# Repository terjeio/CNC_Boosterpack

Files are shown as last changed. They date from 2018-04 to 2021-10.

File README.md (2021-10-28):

## CNC BoosterPack for Texas Instruments LaunchPads

A BoosterPack that provides 3-axis motor support for some LaunchPads, driver code for [grblHAL](https://github.com/grblHAL) is available for [MSP432P401R](https://github.com/grblHAL/MSP432P401R), [MSP432E401Y](https://github.com/grblHAL/MSP432E401Y), Tiva C\([EK-TM4C123GXL](https://github.com/grblHAL/TM4C123) and [EK-TM4C1294XL](https://github.com/grblHAL/TM4C1294)\) and [MSP430F5529](https://github.com/grblHAL/MSP430F5529).

Prototype "motherboards" has been made for ESP32, STM32F103 \(Bluepill\) and SAMD21 \(MKRZERO\) development boards allowing the CNC BoosterPack to be used with these, I may add them later.

**NOTE:** design files are in [KiCad 5](http://www.kicad.org/) format!

**Features:**

* 3-axis motor support with separate enable for Z and X,Y \(X,Y has a single enable signal\). Trinamic version has separate enable for all axes.

* On-board sockets for Polulu style motor driver modules (A4998 and DRV8825). Separate version for Trinamic drivers \(initially TMC2130\).

* Opto-coupled limit and signal inputs (X, Y, Z, Probe, Reset, Door, Feed Hold and Cycle Start) with 5V drive voltage.

* Opto-coupled signal outputs \(Spindle on, Spindle direction, Flood and Mist\) with jumper selectable drive voltage \(5V internal or externally supplied\). Outputs are open drain \(2N7002\) capable of draining 200mA \(up to 300mA depending on 2N7002 variant\), enough to drive most relays directly. Outputs can be made opto-isolated via jumper settings.

* PWM output for spindle speed control, unbuffered.

* One I2C port with jumper selectable drive voltage \(3.3V or 5V\). This is complemented with a GPIO pin that may be used as an interrupt source, eg. for a I2C-based keypad.

* Two GPIO ports, one with four pins and one with two. Two-pin GPIO-port may be used as secondary UART input, eg. for MPG control.

* Optional on-board EEPROM for persistent storage of settings.

Separate version for Trinamic TMC2130 drivers added, onboard I2C \<\> SPI bridge for driver control. 4-layer board.
A small batch of the Trinamic version has been made, good progress made on [I2C \<\> SPI bridge firmware](https://github.com/terjeio/Trinamic_TMC2130_I2C_SPI_Bridge). Driver monitoring has been delegated to the bridge prosessor, a couple of additional datagrams will be implemented to facilitate support for this in the grblHAL-driver - first out will be for MSP432.

Both designs are now reduced in size so two boards may be mounted on TMC129 or MSP432E401Y LaunchPads for controlling up to 6-axes. 

I have a few bare boards for sale at cost if anyone is interested. The "standard - non-Trinamic" boards I have available is the larger revision 1.0. 

Detailed documentation to follow.

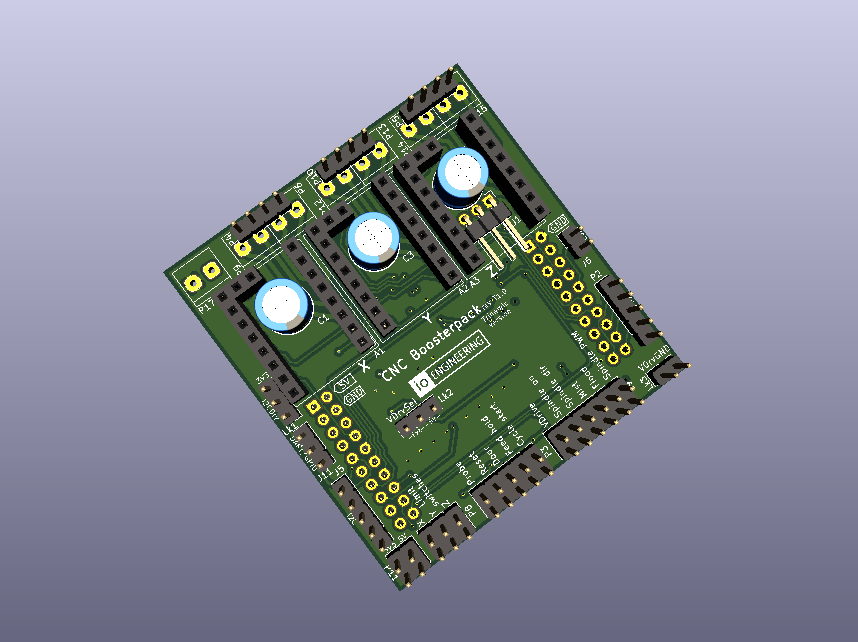
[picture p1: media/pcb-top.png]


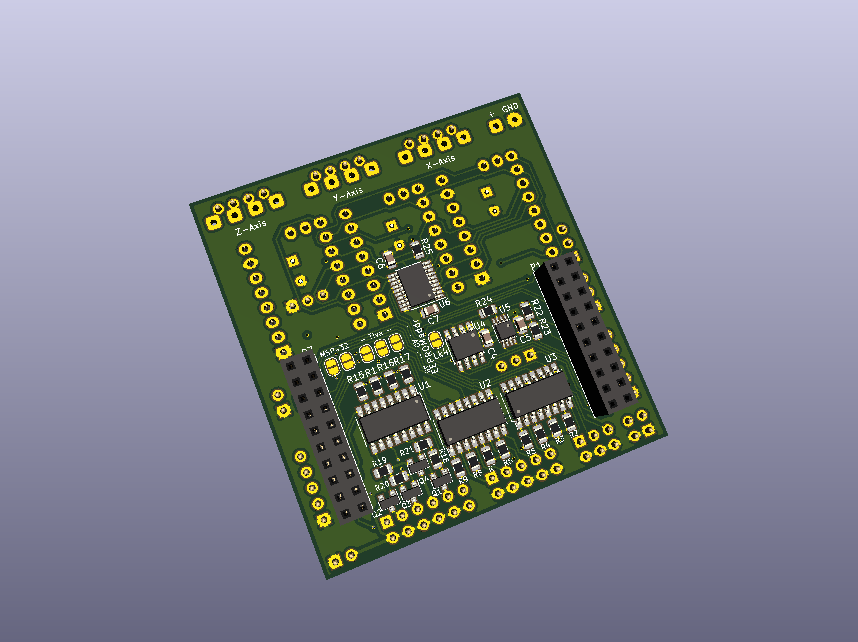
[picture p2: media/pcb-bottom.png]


---

## Bonus design: Polulu style motor driver "dummy"

* with buffered \(open drain\) outputs for external drivers like DQ542MA.

**NOTE:** output signals are inverted

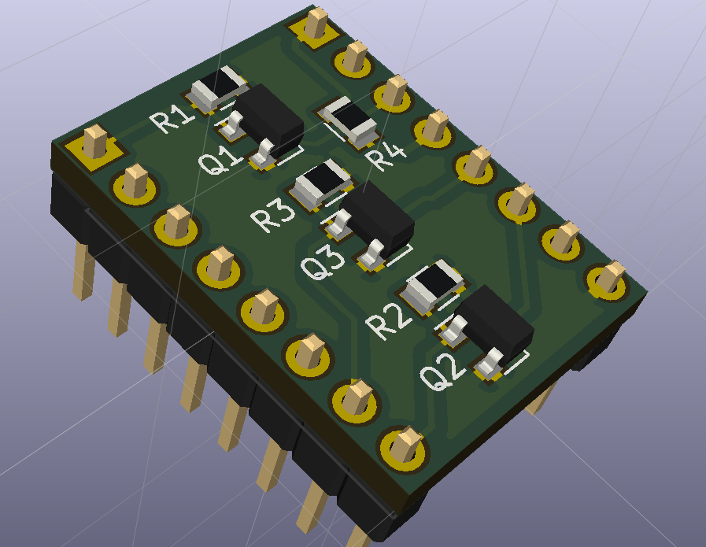
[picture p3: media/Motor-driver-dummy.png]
Dummy PCB


---

## Bonus design II: BLDC Motor driver board, 3.3V (or 5V) PWM to 0 - 10V DC conversion

* with opto-coupled PWM input.

* PCB layout matches WSS55 BLDC Driver connector

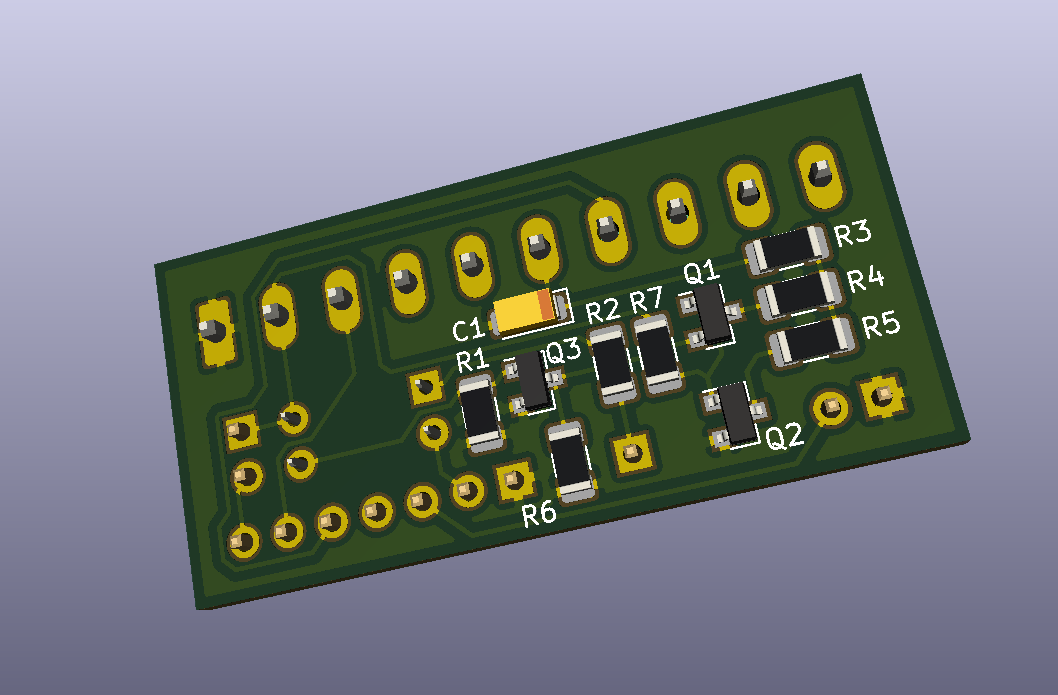
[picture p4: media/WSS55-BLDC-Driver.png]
BLDC Motor Driver PCB


---
2021-10-28

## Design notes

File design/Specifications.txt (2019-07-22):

CNC BoosterPack Rev 1.0

3-axis CNC addon for Texas Instruments LaunchPads with 40 pin interface.

Support for my HALified version of GRBL (based on 1.1), currently drivers has been made for MSP432 (black version), Tiva C and MSP430F2955.
NOTE: firmware is built with CCS 6.1, MSP432 driver is 100% CMSIS based.

Opto-coupled inputs, NC switches recommended.

Opto-coupled outputs with 200mA open drain drive for spindle on, spindle direction, flood and mist.
Can drive most relays and solenoids directly. 
Output section can be powered from internal 3V3 or 5V source, or from external source.
If powered from external source outputs can be made opto-isolated via jumper setting.

PWM-output for spindle speed currently directly connected to MCU pin (could be changed to open drain).

I2C (IIC) interface with selectable voltage level (3V3 or 5V) via level shifter, dedicated interrupt input.
I2C pinout compatible with my 4x4 keyboard project, supports jogging etc.

Optional EEPROM for configuration settings for MCUs with no internal EEPROM.

Polulu 8825 motor driver breakout board compatible. Fault signal routed to GPIO input.

Considered for later revision:

Break out SPI interface and add full support for Trinamic motor drivers.
Optional (SPI) DAC for motor speed (laser power) control.

This might require a 4-layer PCB and also solving the pinout cabal...

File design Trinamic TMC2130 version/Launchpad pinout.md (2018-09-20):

 ## LaunchPad GRBL pin assignments for CNC Boosterpack rev1.0

 ## Tiva C \(TM4C123G\)

```
                      3v3 [] [] VBUS (5v)             Limit Z PF2 [] [] GND
                      PB5 [] [] GND                   Limit Y PF3 [] [] PB2 Spindle PWM
       UART2 RX/GPIO4 PB0 [] [] PD0                     Reset PB3 [] [] PE0 Limit X
       UART2 TX/GPIO5 PB1 [] [] PD1 Step X        Safety Door PC4 [] [] PF0 Stepper disable Z
  Keypad strobe/GPIO6 PE4 [] [] PD2 Step Y          Feed Hold PC5 [] [] RST
                      PE5 [] [] PD3 Step Z        Cycle Start PC6 [] [] PB7 Dir X
                Dir Z PB4 [] [] PE1 Stepper disable XY        PC7 [] [] PB6 Dir Y
                Probe PA5 [] [] PE2 Spindle enable      Flood PD6 [] [] PA4 GPIO1
               I2CSCL PA6 [] [] PE3 Spindle direction    Mist PD7 [] [] PA3 GPIO2
               I2CSDA PA7 [] [] PF1                 RTS/GPIO0 PF4 [] [] PA2 GPIO3
```
__NOTE__: Remove R9 and R10!

With shorts - Limit X (R10): PE0 -> PF1, Reset (R11): PB3 -> PC7

## Tiva C \(TM4C1294\) Boosterpack1

```
                      3v3 [] [] VBUS (5v)             Limit Z PF1 [] [] GND
                      PE4 [] [] GND                   Limit Y PF2 [] [] PM3 Spindle PWM
       UART7 RX/GPIO4 PC4 [] [] PE0                     Reset PF3 [] [] PH2 Limit X
       UART7 TX/GPIO5 PC5 [] [] PE1 Step X        Safety Door PG0 [] [] PH3 Stepper disable Z
  Keypad strobe/GPIO6 PC6 [] [] PE2 Step Y          Feed Hold PL4 [] [] RST
                      PE5 [] [] PE3 Step Z        Cycle Start PL5 [] [] PD1 Dir X
                Dir Z PD3 [] [] PD7 Stepper disable XY        PL0 [] [] PD0 Dir Y
                Probe PC7 [] [] PA6 Spindle enable      Flood PL1 [] [] PN2 GPIO1
               I2CSCL PB2 [] [] PM4 Spindle direction    Mist PL2 [] [] PN3 GPIO2
               I2CSDA PB3 [] [] PM5                 RTS/GPIO0 PL3 [] [] PP3 GPIO3
```

## Tiva C \(TM4C1294\) Boosterpack2

```
                      3v3 [] [] VBUS (5v)             Limit Z PG1 [] [] GND
                      PD2 [] [] GND                   Limit Y PK4 [] [] PM7 Spindle PWM
       UART6 RX/GPIO4 PP0 [] [] PB4                     Reset PK5 [] [] PP5 Limit X
       UART6 TX/GPIO5 PP1 [] [] PB5 Step X        Safety Door PM0 [] [] PA7 Stepper disable Z
  Keypad strobe/GPIO6 PD4 [] [] PK0 Step Y          Feed Hold PM1 [] [] RST
                      PD5 [] [] PK1 Step Z        Cycle Start PM2 [] [] PQ2 Dir X
                Dir Z PQ0 [] [] PK2 Stepper disable XY        PH0 [] [] PQ3 Dir Y
                Probe PP4 [] [] PK3 Spindle enable      Flood PH1 [] [] PP3 GPIO1
               I2CSCL PN5 [] [] PA4 Spindle direction    Mist PK6 [] [] PQ1 GPIO2
               I2CSDA PN4 [] [] PA5                 RTS/GPIO0 PK7 [] [] PM6 GPIO3
```

## MSP430F5529

```
                      3v3 [] [] VBUS (5v)            Limit Z P2.5 [] [] GND
                     P6.5 [] [] GND                  Limit Y P2.4 [] [] P2.0 Spindle PWM
      UART2 RX/GPIO4 P3.4 [] [] P6.0                   Reset P1.5 [] [] P2.2 Limit X
      UART2 TX/GPIO5 P3.3 [] [] P6.1 Step X      Safety Door P1.4 [] [] P7.4 Stepper disable Z
 Keypad strobe/GPIO6 P1.6 [] [] P6.2 Step Y        Feed Hold P1.3 [] [] RST
                     P6.6 [] [] P6.3 Step Z      Cycle Start P1.2 [] [] P3.0 Dir X
               Dir Z P3.2 [] [] P6.4 Stepper disable XY      P4.3 [] [] P3.1 Dir Y
               Probe P2.7 [] [] P7.0 Spindle enable    Flood P4.0 [] [] P2.6 GPIO1
              I2CSCL P4.2 [] [] P3.6 Spindle direction  Mist P3.7 [] [] P2.3 GPIO2
              I2CSDA P4.1 [] [] P3.5               RTS/GPIO0 P8.2 [] [] P8.1 GPIO3
```

## MSP432P401R

```
                      3v3 [] [] VBUS (5v)            Limit Z P2.7 [] [] GND
                     P6.0 [] [] GND                  Limit Y P2.6 [] [] P2.5 Spindle PWM
      UART2 RX/GPIO4 P3.2 [] [] P6.1                   Reset P2.4 [] [] P3.0 Limit X
      UART2 TX/GPIO5 P3.3 [] [] P4.0 Step X      Safety Door P5.6 [] [] P5.7 Stepper disable Z
 Keypad strobe/GPIO6 P4.1 [] [] P4.2 Step Y        Feed Hold P6.6 [] [] RST
                     P4.3 [] [] P4.4 Step Z      Cycle Start P6.7 [] [] P1.6 Dir X
               Dir Z P1.5 [] [] P4.5 Stepper disable XY      P2.3 [] [] P1.7 Dir Y
               Probe P4.6 [] [] P4.7 Spindle enable    Flood P5.1 [] [] P5.0 GPIO1
              I2CSCL P6.5 [] [] P5.4 Spindle direction  Mist P3.5 [] [] P5.2 GPIO2
              I2CSDA P6.4 [] [] P5.5               RTS/GPIO0 P3.7 [] [] P3.6 GPIO3
```
With shorts - Reset (R12): P2.4 -> P6.0, Safety Door (R13): P5.6 -> P6.1, Limit X (R14): P3.0 -> P2.3

---

## Stepper drivers

### A4998 - requires 3V3 on VDD pin
```
MS1     MS2     MS3     Microstep resolution
Low 	Low 	Low 	Full step
High 	Low 	Low 	Half step
Low 	High 	Low 	Quarter step
High 	High 	Low 	Eighth step
High 	High 	High 	Sixteenth step
```
https://www.pololu.com/product/1182

### DRV8825
```
MS1     MS2     MS3     Microstep resolution
Low 	Low 	Low 	Full step
High 	Low 	Low 	Half step
Low 	High 	Low 	1/4 step
High 	High 	Low 	1/8 step
Low 	Low 	High 	1/16 step
High 	Low 	High 	1/32 step
Low 	High 	High 	1/32 step
High 	High 	High 	1/32 step
```
https://www.pololu.com/product/2133

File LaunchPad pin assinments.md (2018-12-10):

 ## LaunchPad grblHAL pin assignments for CNC Boosterpack rev1.0

 ### Tiva C \(TM4C123G\)

```
                      3v3 [] [] VBUS (5v)             Limit Z PF2 [] [] GND
                      PB5 [] [] GND                   Limit Y PF3 [] [] PB2 Spindle PWM
       UART2 RX/GPIO4 PB0 [] [] PD0                     Reset PB3 [] [] PE0 Limit X
       UART2 TX/GPIO5 PB1 [] [] PD1 Step X        Safety Door PC4 [] [] PF0 Stepper disable Z
  Keypad strobe/GPIO6 PE4 [] [] PD2 Step Y          Feed Hold PC5 [] [] RST
                      PE5 [] [] PD3 Step Z        Cycle Start PC6 [] [] PB7 Dir X
                Dir Z PB4 [] [] PE1 Stepper disable XY        PC7 [] [] PB6 Dir Y
                Probe PA5 [] [] PE2 Spindle enable      Flood PD6 [] [] PA4 GPIO1
               I2CSCL PA6 [] [] PE3 Spindle direction    Mist PD7 [] [] PA3 GPIO2
               I2CSDA PA7 [] [] PF1                 RTS/GPIO0 PF4 [] [] PA2 GPIO3
```
__NOTE__: Remove R9 and R10! Q1, Q2 and Q3 may also be removed (depending on limit switches configuration) as they have inbuilt pull down resistors.

With shorts - Limit X (R10): PE0 -> PF1, Reset (R11): PB3 -> PC7

---

### Tiva C \(TM4C1294\) and MSP432E401Y
 
 Boosterpack 1

```
                      3v3 [] [] VBUS (5v)             Limit Z PF1 [] [] GND
                      PE4 [] [] GND                   Limit Y PF2 [] [] PM3 Spindle PWM
       UART7 RX/GPIO4 PC4 [] [] PE0                     Reset PF3 [] [] PH2 Limit X
       UART7 TX/GPIO5 PC5 [] [] PE1 Step X        Safety Door PG0 [] [] PH3 Stepper disable Z
  Keypad strobe/GPIO6 PC6 [] [] PE2 Step Y          Feed Hold PL4 [] [] RST
                      PE5 [] [] PE3 Step Z        Cycle Start PL5 [] [] PD1 Dir X
                Dir Z PD3 [] [] PD7 Stepper disable XY        PL0 [] [] PD0 Dir Y
                Probe PC7 [] [] PA6 Spindle enable      Flood PL1 [] [] PN2 GPIO1
               I2CSCL PB2 [] [] PM4 Spindle direction    Mist PL2 [] [] PN3 GPIO2
               I2CSDA PB3 [] [] PM5                 RTS/GPIO0 PL3 [] [] PP3 GPIO3
```
Boosterpack 2, ABC-axes

```
                      3v3 [] [] VBUS (5v)             Limit B PG1 [] [] GND
                      PD2 [] [] GND                   Limit A PK4 [] [] PM7 Spindle PWM
          U6 RX/GPIO4 PP0 [] [] PB4                     Reset PK5 [] [] PP5 Limit C
          U6 TX/GPIO5 PP1 [] [] PB5 Step C        Safety Door PM0 [] [] PA7 Stepper disable B
  Keypad strobe/GPIO6 PD4 [] [] PK0 Step A          Feed Hold PM1 [] [] RST
                      PD5 [] [] PK1 Step B        Cycle Start PM2 [] [] PQ2 Dir C (PA3)
                Dir B PQ0 [] [] PK2 Stepper disable AC        PH0 [] [] PQ3 Dir A (PA2)
                Probe PP4 [] [] PK3 Spindle enable      Flood PH1 [] [] PP3 GPIO1
               I2CSCL PN5 [] [] PA4 Spindle direction    Mist PK6 [] [] PQ1 GPIO2
               I2CSDA PN4 [] [] PA5                 RTS/GPIO0 PK7 [] [] PM6 GPIO3
```

Boosterpack2, SD Card - TM4C1294 \(SSI0\)

```
                      3v3 [] [] VBUS (5v)                     PG1 [] [] GND
                      PD2 [] [] GND                           PK4 [] [] PM7
                      PP0 [] [] PB4                           PK5 [] [] PP5 CS
                      PP1 [] [] PB5                           PM0 [] [] PA7
                      PD4 [] [] PK0                           PM1 [] [] RST
                      PD5 [] [] PK1                           PM2 [] [] PQ2
                      PQ0 [] [] PK2                           PH0 [] [] PQ3 CLK        
                      PP4 [] [] PK3                           PH1 [] [] PP3
                      PN5 [] [] PA4 MOSI                      PK6 [] [] PQ1
                      PN4 [] [] PA5 SOMI                      PK7 [] [] PM6
```

Boosterpack2, SD Card - MSP432E401Y \(SSI3\)

```
                      3v3 [] [] VBUS (5v)                     PG1 [] [] GND
                      PD2 [] [] GND                           PK4 [] [] PM7
                      PP0 [] [] PB4                           PK5 [] [] PP5 CS
                      PP1 [] [] PB5                           PM0 [] [] PA7
                      PD4 [] [] PK0                           PM1 [] [] RST
                      PD5 [] [] PK1                           PM2 [] [] PQ2 MOSI
                  CLK PQ0 [] [] PK2                           PH0 [] [] PQ3 SOMI
                      PP4 [] [] PK3                           PH1 [] [] PP3
                      PN5 [] [] PA4                           PK6 [] [] PQ1
                      PN4 [] [] PA5                           PK7 [] [] PM6
```

---

### MSP430F5529

```
                      3v3 [] [] VBUS (5v)            Limit Z P2.5 [] [] GND
                     P6.5 [] [] GND                  Limit Y P2.4 [] [] P2.0 Spindle PWM
      UART2 RX/GPIO4 P3.4 [] [] P6.0                   Reset P1.5 [] [] P2.2 Limit X
      UART2 TX/GPIO5 P3.3 [] [] P6.1 Step X      Safety Door P1.4 [] [] P7.4 Stepper disable Z
 Keypad strobe/GPIO6 P1.6 [] [] P6.2 Step Y        Feed Hold P1.3 [] [] RST
                     P6.6 [] [] P6.3 Step Z      Cycle Start P1.2 [] [] P3.0 Dir X
               Dir Z P3.2 [] [] P6.4 Stepper disable XY      P4.3 [] [] P3.1 Dir Y
               Probe P2.7 [] [] P7.0 Spindle enable    Flood P4.0 [] [] P2.6 GPIO1
              I2CSCL P4.2 [] [] P3.6 Spindle direction  Mist P3.7 [] [] P2.3 GPIO2
              I2CSDA P4.1 [] [] P3.5               RTS/GPIO0 P8.2 [] [] P8.1 GPIO3
```

---

### MSP432P401R

```
                      3v3 [] [] VBUS (5v)            Limit Z P2.7 [] [] GND
                     P6.0 [] [] GND                  Limit Y P2.6 [] [] P2.5 Spindle PWM
      UART2 RX/GPIO4 P3.2 [] [] P6.1                   Reset P2.4 [] [] P3.0 Limit X
      UART2 TX/GPIO5 P3.3 [] [] P4.0 Step X      Safety Door P5.6 [] [] P5.7 Stepper disable Z
 Keypad strobe/GPIO6 P4.1 [] [] P4.2 Step Y        Feed Hold P6.6 [] [] RST
                     P4.3 [] [] P4.4 Step Z      Cycle Start P6.7 [] [] P1.6 Dir X
               Dir Z P1.5 [] [] P4.5 Stepper disable XY      P2.3 [] [] P1.7 Dir Y
               Probe P4.6 [] [] P4.7 Spindle enable    Flood P5.1 [] [] P5.0 GPIO1
              I2CSCL P6.5 [] [] P5.4 Spindle direction  Mist P3.5 [] [] P5.2 GPIO2
              I2CSDA P6.4 [] [] P5.5               RTS/GPIO0 P3.7 [] [] P3.6 GPIO3
```
With shorts - Reset (R12): P2.4 -> P6.0, Safety Door (R13): P5.6 -> P6.1, Limit X (R14): P3.0 -> P2.3

---

### Stepper drivers

#### A4998

**NOTE:** requires 3V3 on VDD pin supplied from GPIO output

```
MS1     MS2     MS3     Microstep resolution
Low 	Low 	Low 	Full step
High 	Low 	Low 	Half step
Low 	High 	Low 	Quarter step
High 	High 	Low 	Eighth step
High 	High 	High 	Sixteenth step
```
https://www.pololu.com/product/1182

#### DRV8825
```
MS1     MS2     MS3     Microstep resolution
Low 	Low 	Low 	Full step
High 	Low 	Low 	Half step
Low 	High 	Low 	1/4 step
High 	High 	Low 	1/8 step
Low 	Low 	High 	1/16 step
High 	Low 	High 	1/32 step
Low 	High 	High 	1/32 step
High 	High 	High 	1/32 step
```
https://www.pololu.com/product/2133

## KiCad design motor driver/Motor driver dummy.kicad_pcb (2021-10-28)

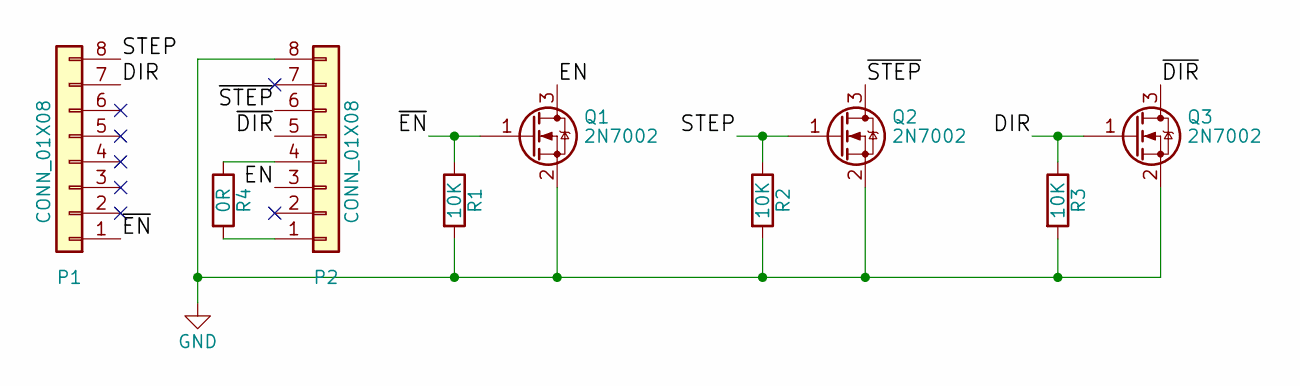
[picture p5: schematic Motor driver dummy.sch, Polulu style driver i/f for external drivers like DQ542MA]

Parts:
P1, P2: CONN_01X08; PinHeader_1x08_P2.54mm_Vertical
Q1, Q2, Q3: 2N7002; SOT-23
R1, R2, R3: 10K; R_0805_2012Metric
R4: 0R; R_0805_2012Metric

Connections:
/DIR: P1.7, Q3.1 (G), R3.1
/EN: P2.3, Q1.3 (D)
/STEP: P1.8, Q2.1 (G), R2.1
/~DIR: P2.5, Q3.3 (D)
/~EN: P1.1, Q1.1 (G), R1.1
/~STEP: P2.6, Q2.3 (D)
GND: P2.8, Q1.2 (S), Q2.2 (S), Q3.2 (S), R1.2, R2.2, R3.2
unnamed: P2.1, R4.2
unnamed: P2.4, R4.1

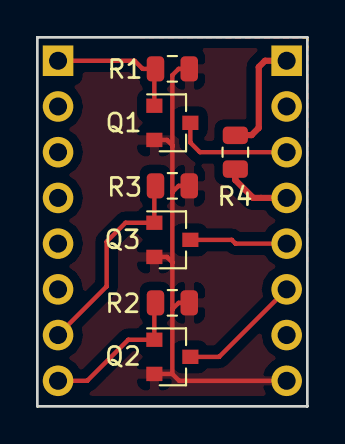
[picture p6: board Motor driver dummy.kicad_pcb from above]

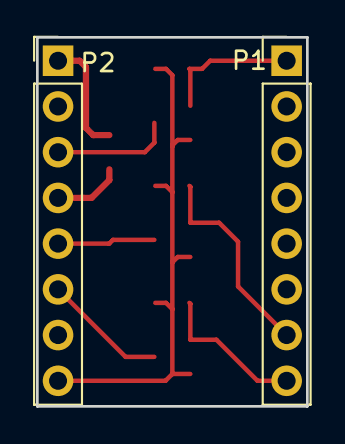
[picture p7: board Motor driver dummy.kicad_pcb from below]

Board: 2 copper layers, 15.0 x 20.5 mm, 9 parts (2 on the bottom side), 9 nets.

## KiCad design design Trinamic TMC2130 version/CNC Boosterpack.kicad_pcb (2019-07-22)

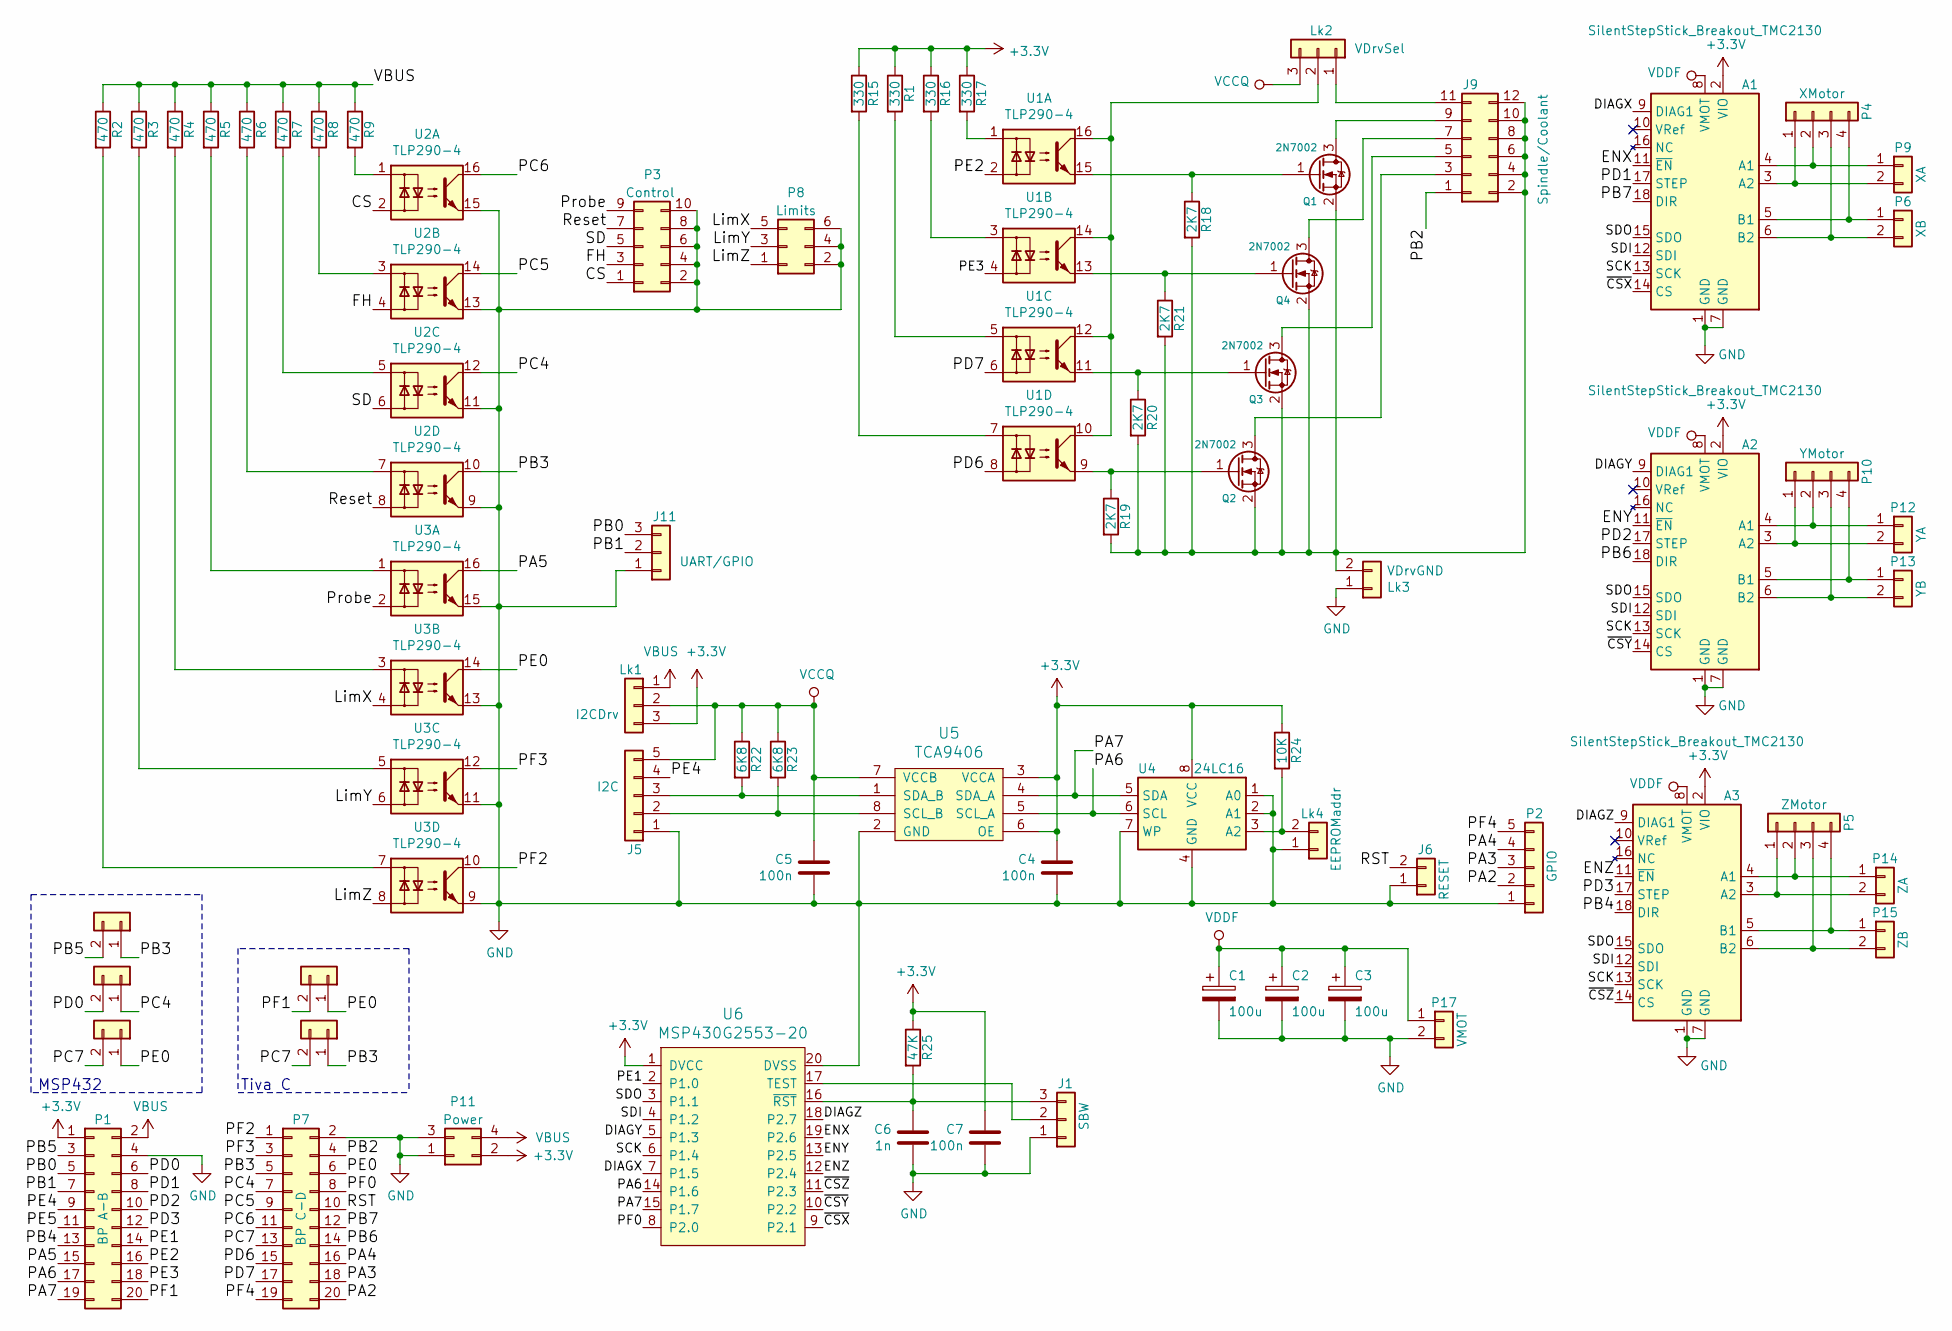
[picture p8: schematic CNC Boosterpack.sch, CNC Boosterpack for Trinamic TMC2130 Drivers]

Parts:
A1, A2, A3: SilentStepStick_Breakout_TMC2130; SilentStepStick_TMC2130
C1, C2, C3: 100u; CP_Radial_D8.0mm_P3.50mm
C4, C5, C7: 100n; C_0805_2012Metric
C6: 1n; C_0805_2012Metric
J1: SBW; PinHeader_1x03_P2.54mm_Horizontal
J2, J3, J12, J13, J14: Lk; SolderJumper-2_P1.3mm_Open_RoundedPad1.0x1.5mm
J5: I2C; PinHeader_1x05_P2.54mm_Vertical
J6: RESET; PinHeader_1x02_P2.54mm_Vertical
J9: Spindle/Coolant; PinHeader_2x06_P2.54mm_Vertical
J11: UART/GPIO; PinHeader_1x03_P2.54mm_Vertical
Lk1: I2CDrv; PinHeader_1x03_P2.54mm_Vertical
Lk2: VDrvSel; PinHeader_1x03_P2.54mm_Vertical
Lk3: VDrvGND; PinHeader_1x02_P2.54mm_Vertical
Lk4: EEPROMaddr; SolderJumper-2_P1.3mm_Open_RoundedPad1.0x1.5mm
P1: BP A-B; PinSocket_2x10_P2.54mm_Vertical
P2: GPIO; PinHeader_1x05_P2.54mm_Vertical
P3: Control; PinHeader_2x05_P2.54mm_Vertical
P4: XMotor; PinHeader_1x04_P2.54mm_Vertical_Motor
P5: ZMotor; PinHeader_1x04_P2.54mm_Vertical_Motor
P6: XB; CONN_PWR_2P_3.5MM_CAMBLOCK
P7: BP C-D; PinSocket_2x10_P2.54mm_Vertical
P8: Limits; PinHeader_2x03_P2.54mm_Vertical
P9: XA; CONN_PWR_2P_3.5MM_CAMBLOCK
P10: YMotor; PinHeader_1x04_P2.54mm_Vertical_Motor
P11: Power; PinHeader_2x02_P2.54mm_Vertical
P12: YA; CONN_PWR_2P_3.5MM_CAMBLOCK
P13: YB; CONN_PWR_2P_3.5MM_CAMBLOCK
P14: ZA; CONN_PWR_2P_3.5MM_CAMBLOCK
P15: ZB; CONN_PWR_2P_3.5MM_CAMBLOCK
P17: VMOT; CONN_PWR_2P_3.5MM_CAMBLOCK
Q1, Q2, Q3, Q4: 2N7002; SOT-23
R1, R15, R16, R17: 330; R_0805_2012Metric
R2, R3, R4, R5, R6, R7, R8, R9: 470; R_0805_2012Metric
R18, R19, R20, R21: 2K7; R_0805_2012Metric
R22, R23: 6K8; R_0805_2012Metric
R24: 10K; R_0805_2012Metric
R25: 47K; R_0805_2012Metric
U1, U2, U3: TLP290-4; SOP-16_4.4x10.4mm_P1.27mm
U4: 24LC16; SOIC-8_3.9x4.9mm_P1.27mm
U5: TCA9406; SSOP-8_2.95x2.8mm_P0.65mm
U6: MSP430G2553-20; TSSOP-20_4.4x6.5mm_P0.65mm

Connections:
+3V3: A1.2 (VIO), A2.2 (VIO), A3.2 (VIO), C4.1, C7.1, Lk1.3, P1.1, P11.2, R1.1, R15.1, R16.1, R17.1, R24.1, R25.1, U4.8 (VCC), U5.3 (VCCA), U5.6 (OE), U6.1 (DVCC)
/CS: P3.1, U2.2
/DIAGX: A1.9 (DIAG1), U6.7 (P1.5)
/DIAGY: A2.9 (DIAG1), U6.5 (P1.3)
/DIAGZ: A3.9 (DIAG1), U6.18 (P2.7)
/ENX: A1.11 (~EN), U6.19 (P2.6)
/ENY: A2.11 (~EN), U6.13 (P2.5)
/ENZ: A3.11 (~EN), U6.12 (P2.4)
/FH: P3.3, U2.4
/LimX: P8.5, U3.4
/LimY: P8.3, U3.6
/LimZ: P8.1, U3.8
/PA2: P2.2, P7.20
/PA3: P2.3, P7.18
/PA4: P2.4, P7.16
/PA5: P1.15, U3.16
/PA6: P1.17, U4.6 (SCL), U5.5 (SCL_A), U6.14 (P1.6)
/PA7: P1.19, U4.5 (SDA), U5.4 (SDA_A), U6.15 (P1.7)
/PB0: J11.3, P1.5
/PB1: J11.2, P1.7
/PB2: J9.1, P7.4
/PB3: J2.1, J14.1, P7.5, U2.10
/PB4: A3.18 (DIR), P1.13
/PB5: J2.2, P1.3
/PB6: A2.18 (DIR), P7.14
/PB7: A1.18 (DIR), P7.12
/PC4: J3.1, P7.7, U2.12
/PC5: P7.9, U2.14
/PC6: P7.11, U2.16
/PC7: J12.2, J14.2, P7.13
/PD0: J3.2, P1.6
/PD1: A1.17 (STEP), P1.8
/PD2: A2.17 (STEP), P1.10
/PD3: A3.17 (STEP), P1.12
/PD6: P7.15, U1.8
/PD7: P7.17, U1.6
/PE0: J12.1, J13.1, P7.6, U3.14
/PE1: P1.14, U6.2 (P1.0)
/PE2: P1.16, U1.2
/PE3: P1.18, U1.4
/PE4: J5.4, P1.9
/PE5: P1.11
/PF0: P7.8, U6.8 (P2.0)
/PF1: J13.2, P1.20
/PF2: P7.1, U3.10
/PF3: P7.3, U3.12
/PF4: P2.5, P7.19
/Probe: P3.9, U3.2
/RST: J6.2, P7.10
/Reset: P3.7, U2.8
/SCK: A1.13 (SCK), A2.13 (SCK), A3.13 (SCK), U6.6 (P1.4)
/SD: P3.5, U2.6
/SDI: A1.12 (SDI), A2.12 (SDI), A3.12 (SDI), U6.4 (P1.2)
/SDO: A1.15 (SDO), A2.15 (SDO), A3.15 (SDO), U6.3 (P1.1)
/~CSX: A1.14 (CS), U6.9 (P2.1)
/~CSY: A2.14 (CS), U6.10 (P2.2)
/~CSZ: A3.14 (CS), U6.11 (P2.3)
GND: A1.1 (GND), A1.7 (GND), A2.1 (GND), A2.7 (GND), A3.1 (GND), A3.7 (GND), C1.2, C2.2, C3.2, C4.2, C5.2, C6.2, C7.2, J1.1, J5.1, J6.1, J11.1, Lk3.1, Lk4.1, P1.4, P2.1, P3.2, P3.4, P3.6, P3.8, P3.10, P7.2, P8.2, P8.4, P8.6, P11.1, P11.3, P17.2, U2.9, U2.11, U2.13, U2.15, U3.9, U3.11, U3.13, U3.15, U4.1 (A0), U4.2 (A1), U4.4 (GND), U4.7 (WP), U5.2 (GND), U6.20 (DVSS)
unnamed: A1.3 (A2), P4.1, P9.2
unnamed: A1.4 (A1), P4.2, P9.1
unnamed: A1.5 (B1), P4.4, P6.1
unnamed: A1.6 (B2), P4.3, P6.2
unnamed: A2.3 (A2), P10.1, P12.2
unnamed: A2.4 (A1), P10.2, P12.1
unnamed: A2.5 (B1), P10.4, P13.1
unnamed: A2.6 (B2), P10.3, P13.2
unnamed: A3.3 (A2), P5.1, P14.2
unnamed: A3.4 (A1), P5.2, P14.1
unnamed: A3.5 (B1), P5.4, P15.1
unnamed: A3.6 (B2), P5.3, P15.2
unnamed: C6.1, J1.3, R25.2, U6.16 (~RST~)
unnamed: J1.2, U6.17 (TEST)
unnamed: J5.2, R23.2, U5.8 (SCL_B)
unnamed: J5.3, R22.2, U5.1 (SDA_B)
unnamed: J9.3, Q2.3 (D)
unnamed: J9.5, Q3.3 (D)
unnamed: J9.7, Q4.3 (D)
unnamed: J9.9, Q1.3 (D)
unnamed: J9.2, J9.4, J9.6, J9.8, J9.10, J9.12, Lk3.2, Q1.2 (S), Q2.2 (S), Q3.2 (S), Q4.2 (S), R18.2, R19.2, R20.2, R21.2
unnamed: J9.11, Lk2.1
unnamed: Lk2.2, U1.10, U1.12, U1.14, U1.16
unnamed: Lk4.2, R24.2, U4.3 (A2)
unnamed: Q1.1 (G), R18.1, U1.15
unnamed: Q2.1 (G), R19.1, U1.9
unnamed: Q3.1 (G), R20.1, U1.11
unnamed: Q4.1 (G), R21.1, U1.13
unnamed: R1.2, U1.5
unnamed: R2.2, U3.7
unnamed: R3.2, U3.5
unnamed: R4.2, U3.3
unnamed: R5.2, U3.1
unnamed: R6.2, U2.7
unnamed: R7.2, U2.5
unnamed: R8.2, U2.3
unnamed: R9.2, U2.1
unnamed: R15.2, U1.7
unnamed: R16.2, U1.3
unnamed: R17.2, U1.1
VBUS: Lk1.1, P1.2, P11.4, R2.1, R3.1, R4.1, R5.1, R6.1, R7.1, R8.1, R9.1
VCCQ: C5.1, J5.5, Lk1.2, Lk2.3, R22.1, R23.1, U5.7 (VCCB)
VDDF: A1.8 (VMOT), A2.8 (VMOT), A3.8 (VMOT), C1.1, C2.1, C3.1, P17.1

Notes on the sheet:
MSP432
Tiva C

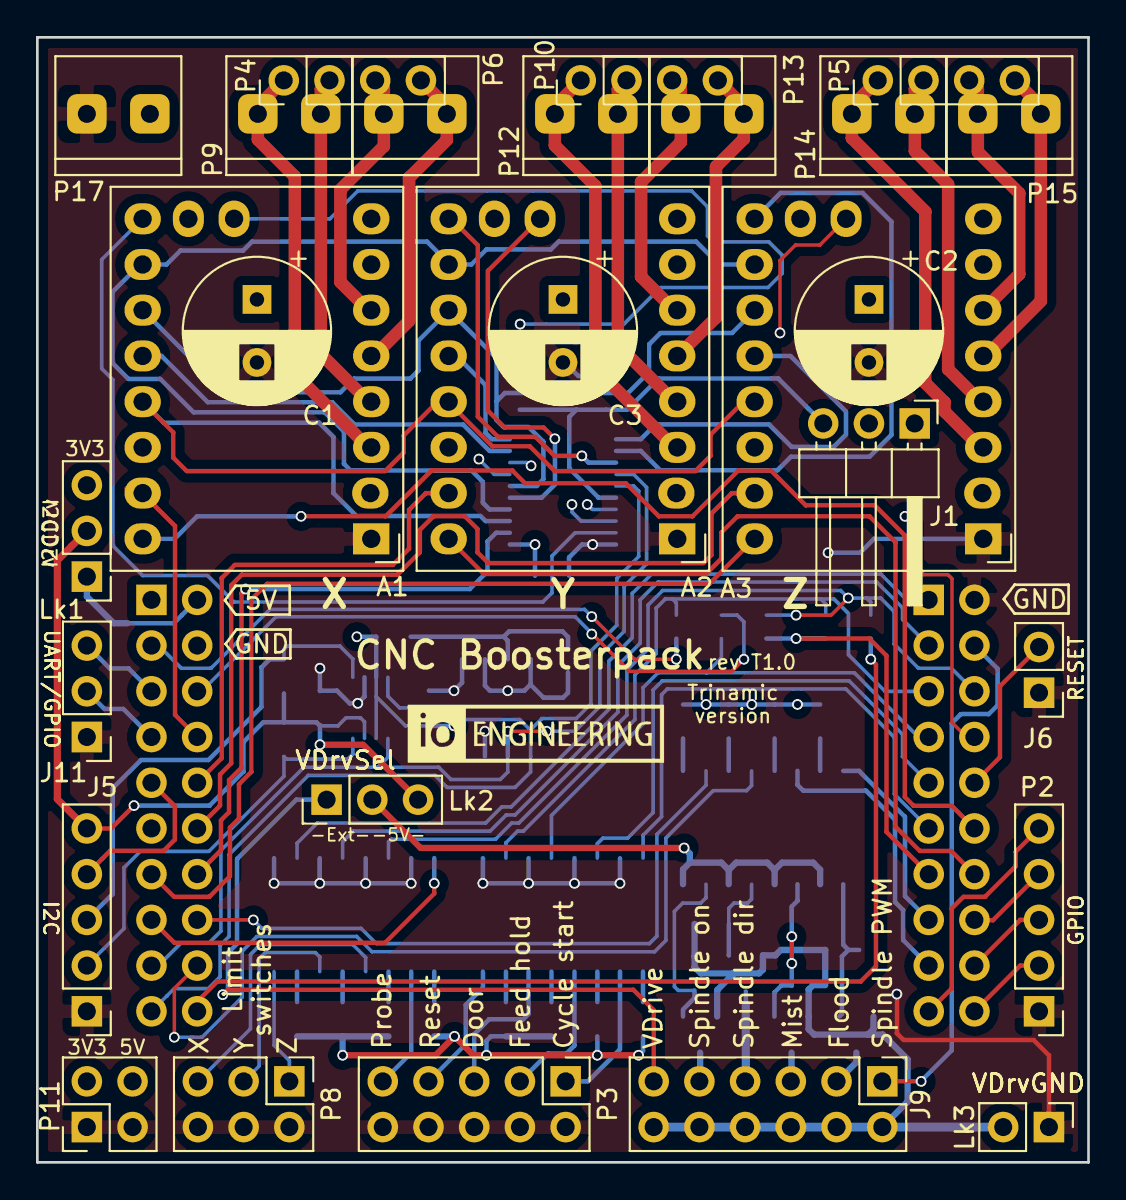
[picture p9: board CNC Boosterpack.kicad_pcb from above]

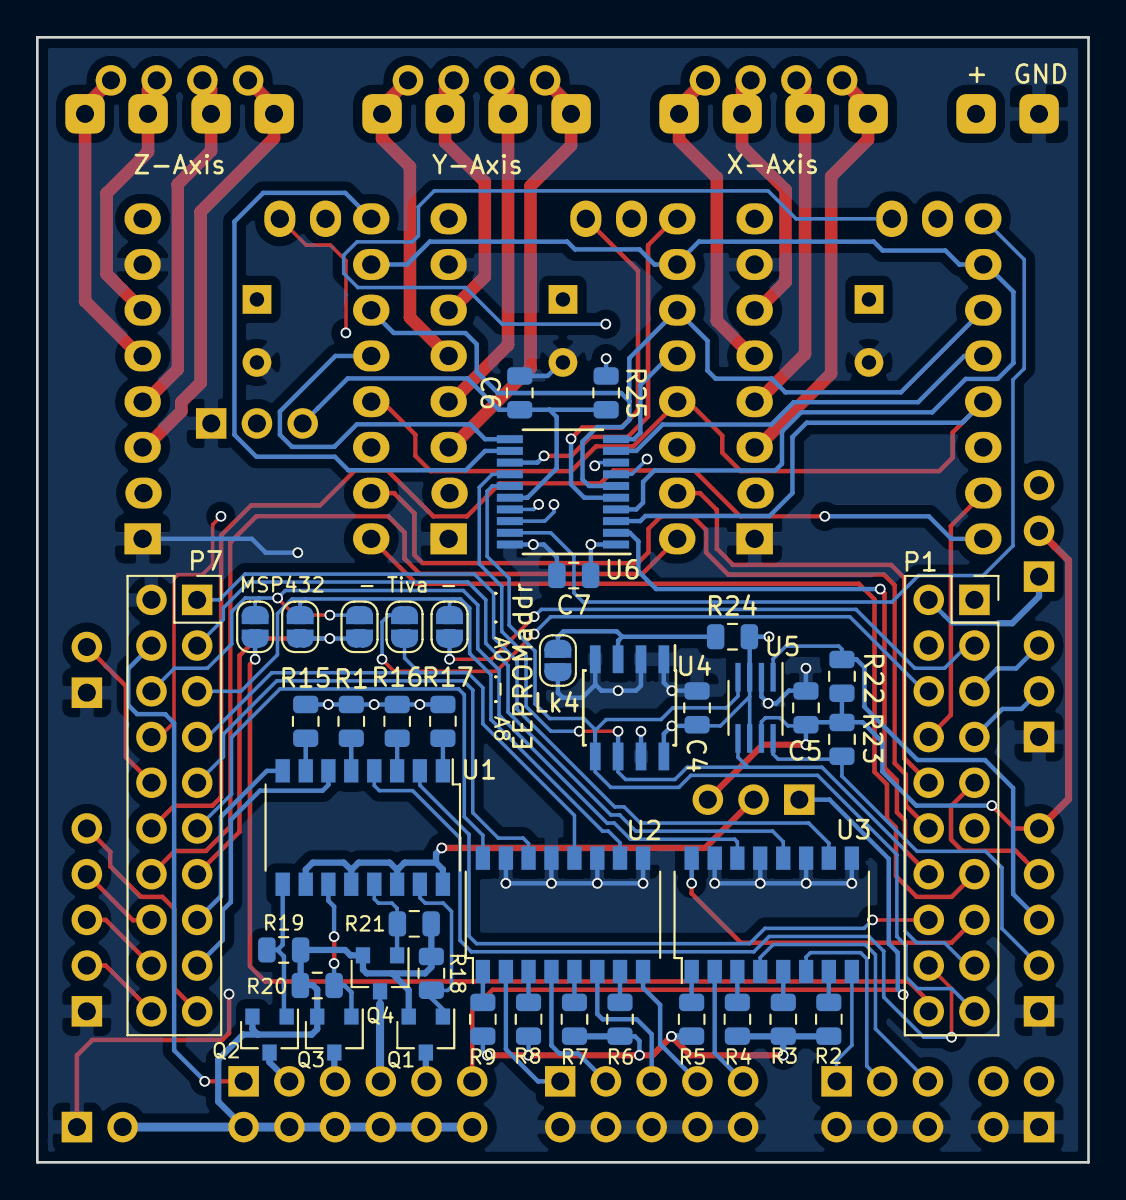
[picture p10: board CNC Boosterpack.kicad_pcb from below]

Board: 4 copper layers, 58.4 x 62.5 mm, 70 parts (42 on the bottom side), 100 nets.

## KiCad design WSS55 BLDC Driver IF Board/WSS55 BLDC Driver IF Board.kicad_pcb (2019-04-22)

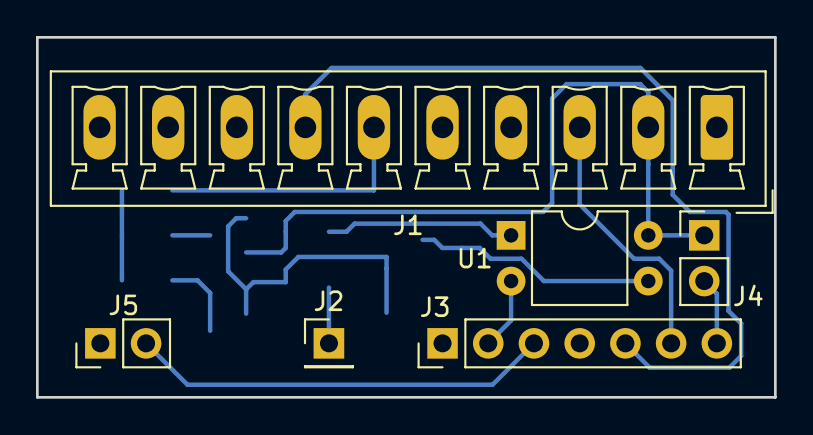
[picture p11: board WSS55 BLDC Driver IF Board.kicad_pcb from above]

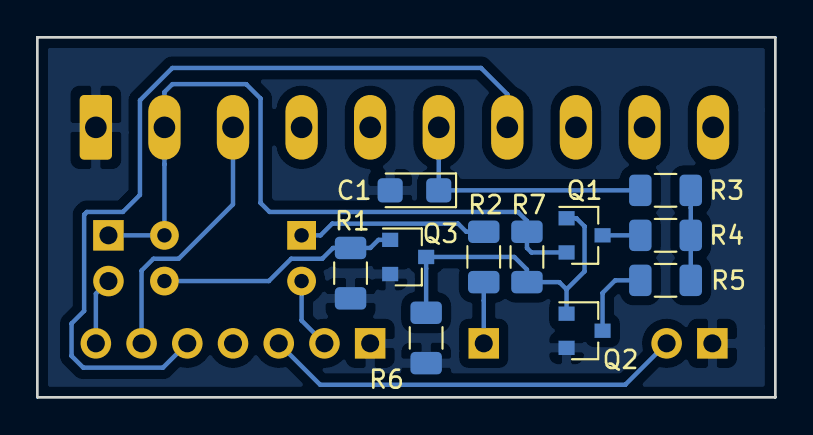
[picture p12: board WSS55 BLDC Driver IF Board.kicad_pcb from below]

Board: 2 copper layers, 41.0 x 20.0 mm, 17 parts (11 on the bottom side), 15 nets.

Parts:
C1: 4u7; CP_EIA-3216-10_Kemet-I
J1: BLDC Driver; PhoenixContact_MCV_1,5_10-G-3.81_1x10_P3.81mm_Vertical
J2: 3V3; PinHeader_1x01_P2.54mm_Vertical
J3: CNC Boosterpack out; PinHeader_1x07_P2.54mm_Vertical
J4: VDrive; PinHeader_1x02_P2.54mm_Vertical
J5: Coolant out; PinHeader_1x02_P2.54mm_Vertical
Q1: IRLML6402; SOT-23
Q2, Q3: 2N7002; SOT-23
R1: 270; R_1206_3216Metric
R2, R4, R5: 220; R_1206_3216Metric
R3: 1K2; R_1206_3216Metric
R6: 10K; R_1206_3216Metric
R7: 820; R_1206_3216Metric
U1: PC817; DIP-4_W7.62mm

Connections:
GND: C1.2, J1.1, J3.1, J5.1, Q2.2, Q3.2, R1.1, R6.2
unnamed: C1.1, J1.6, R3.2
unnamed: J1.2, J4.1, Q1.2, R7.1, U1.4
unnamed: J1.3, J3.6
unnamed: J1.7, J3.5
unnamed: J2.1, R2.1
unnamed: J3.2, U1.2
unnamed: J3.3, J5.2
unnamed: J3.7, J4.2
unnamed: Q1.1, Q2.1, Q3.3, R6.1, R7.2
unnamed: Q1.3, R4.1
unnamed: Q2.3, R5.2
unnamed: Q3.1, R1.2, U1.3
unnamed: R2.2, U1.1
unnamed: R3.1, R4.2, R5.1

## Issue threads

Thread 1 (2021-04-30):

Firmware for MSP430G2553 I2C - SPI Bridge

budgrif, 2021-04-30:
Is the firmware available that is used in the MSP430G2553? I haven't been able to locate it.

terjeio, 2021-04-30:
It is [found here](https://github.com/terjeio/Trinamic_TMC2130_I2C_SPI_Bridge), I'll have to push an update as it is out of sync with the current plugin code. I'll try to do that tomorrow.

terjeio, 2021-05-02:
Updated now, hopefully it is ok. I'll update my lathe to Trinamic drivers a little later - will QC the code then.

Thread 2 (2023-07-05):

Prototype "motherboards" has been made for ESP32, STM32F103 (Bluepill) and SAMD21 (MKRZERO)

psyhlo, 2023-07-05:
As it is written in README
would you share the rest? I would like to use ESP32 or Bluepill

terjeio, 2023-07-06:
I have done a bit of touch-up on the prototypes, these are two layer boards - orginials were one layer with bodge wires.
Note that they are untested and may not work correctly...
The ESP32 and STM103 boards has an option for a SD card socket - I believe I bought them from Farnell. I can try to find the part number if of interest, or perhaps better swap the footprint to whatever you fancy.

Files are in Kicad 5 format:

[ESP32 CNC Mobo.zip](https://github.com/terjeio/CNC_Boosterpack/files/11967001/ESP32.CNC.Mobo.zip)

[MKRZERO CNC Mobo.zip](https://github.com/terjeio/CNC_Boosterpack/files/11967004/MKRZERO.CNC.Mobo.zip)

[STM103F1xx CNC Mobo.zip](https://github.com/terjeio/CNC_Boosterpack/files/11967007/STM103F1xx.CNC.Mobo.zip)

psyhlo, 2023-07-06:
thanks
i'll have a try with them

Closed 2023-07-06.

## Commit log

2018-04-14 CNC Boosterpack desging files
    added files
    [CNC Boosterpack.kicad_pcb, CNC Boosterpack.sch]
2018-04-17 Added bonus design
    Motor driver "dummy" for extenal motor drivers
    [Motor driver dummy x3.kicad_pcb, Motor driver dummy.kicad_pcb, Motor driver dummy.sch]
2018-07-26 Added pin assignments
2018-09-02 Updated readme and silk screen
    [CNC Boosterpack.kicad_pcb]
2018-09-20 Reduced PCB size
    Reduced PCB size to enable two boards to be used with the EK-TM4C1294X
    LaunchPad - providing up to 6 axes of control. Update to driver for this
    LauncPad underway to facilitate IP-streaming of jobs.
    [CNC Boosterpack.kicad_pcb, CNC Boosterpack.sch]
2018-10-26 Added design for Trinamic TMC2130 drivers.
    On-board I2C <> SPI bridge, 4-layer board.
    [CNC Boosterpack.kicad_pcb, CNC Boosterpack.sch]
2019-04-22 Added bonus design for PWM > DC converter
    I am using this to convert a 3.3V PWM spindle signal to 0 - 10V DC for a
    WSS55 BLDC driver. Can be used with 5V PWM signals and other output
    voltages as well. Input is opto-isolated.
    [WSS55 BLDC Driver IF Board.kicad_pcb, WSS55 BLDC Driver IF Board.sch]
2019-07-22 Updated to latest revision
    A small batch of the Trinamic-version PCB has been made, driver
    development in good progress. Marlin-style M-commands will be supported
    including status reports. Grbl protocol extensions allows real-trime
    plotting of data (stallguard value) for simpler tuning.
    [CNC Boosterpack.kicad_pcb, CNC Boosterpack.sch]
2021-10-28 Updated motor driver dummy to KiCad v5 format
    [Motor driver dummy.kicad_pcb, Motor driver dummy.sch]

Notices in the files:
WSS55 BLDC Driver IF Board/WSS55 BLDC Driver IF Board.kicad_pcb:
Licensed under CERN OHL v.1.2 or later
